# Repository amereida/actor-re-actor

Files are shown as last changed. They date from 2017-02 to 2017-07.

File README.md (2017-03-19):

# actor-re-actor

This repository contains all relevant assets and information for building the **actor-re-actor** unit, a modular device designed for the Athens exhibit of Amereida, entitled 

			**amereida 
			phalène 
			latin (south)
			america**. 

There are 9 of these units.

This work was comissioned as part of the **documenta14** project and realized by the [http://amereida.cl](Open City Group) and [http://ead.pucv.cl](The Shcool of Architecture and Design e[ad], ) [http://www.pucv.cl](Pontificia Universidad Católica de Valparaíso).

### General Shcematics

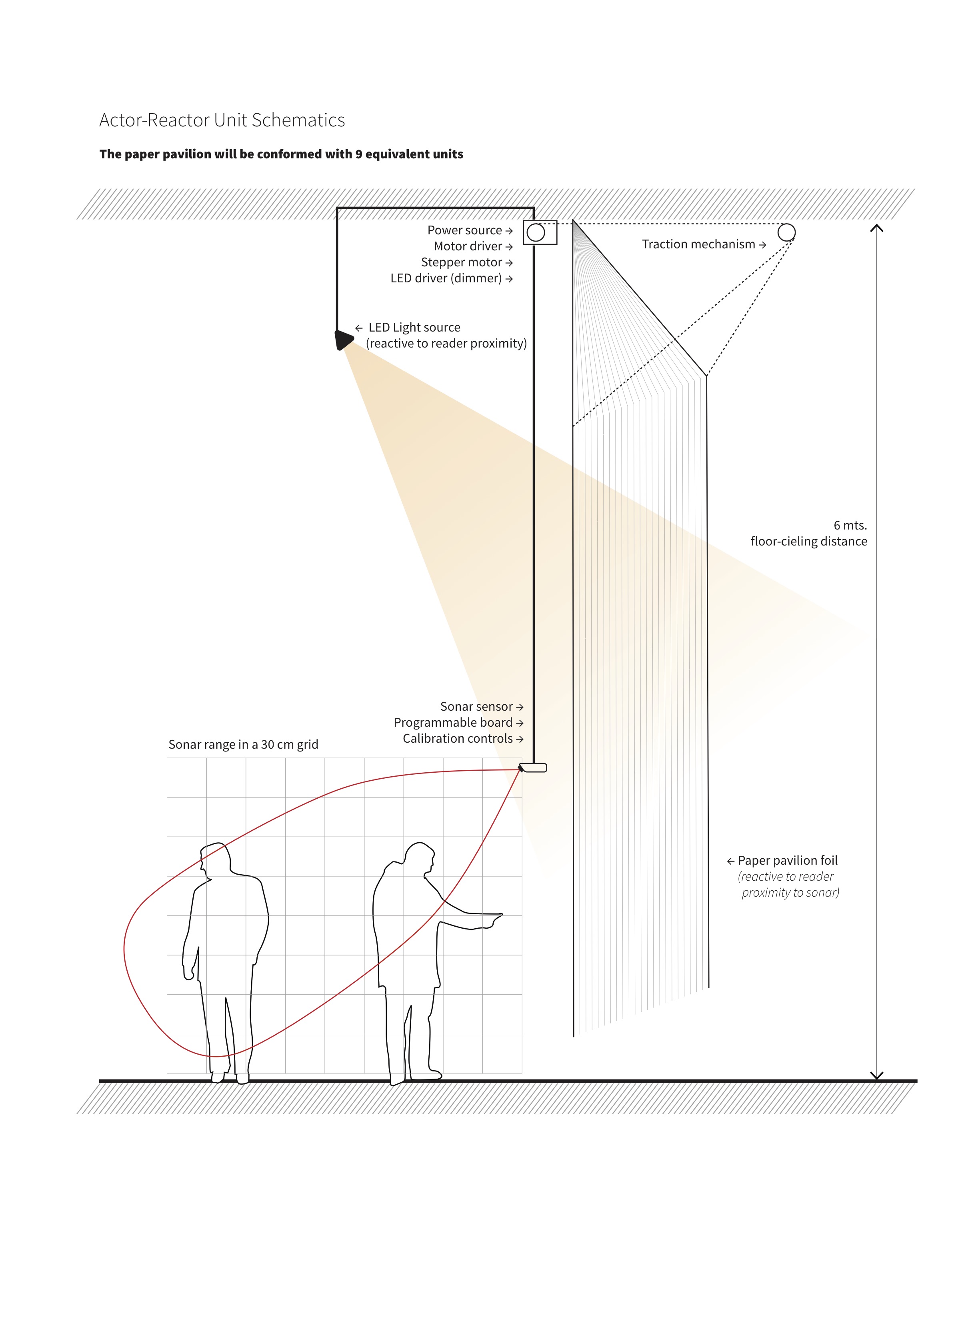
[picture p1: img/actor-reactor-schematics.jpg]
Schema


### Components

1. Actuator Box (inventor files)
	motor-coil (inventor files)
	dimmer (plaques and schematics)
	power & cables (grid)
2. Sensor Box
	Control unit
	Input sensor

### Artistic Statement

     //////////////////////////////////////////////////
     //              //              //              //
     //              //              //              //
     //      1       //       2      //       3      //
     //              //              //              //
     //              //              //              //
     //////////////////////////////////////////////////
     //              //              //              //
     //              //              //              //
     //      4       //       5      //       6      //
     //              //              //              //
     //              //              //              // 
     //////////////////////////////////////////////////
     //              //              //              //
     //              //              //              //
     //      7       //       8      //       9      //
     //              //              //              //
     //              //              //              //     
     //              //              //              //
     //              //              //
     //              //              //

#### 9 Origins, 9 Principles

In this exhibition we ask ourselves for our origin. That is the way of making our content (logos) accessible and open to others, and it is a gesture of hospitality in the first place. Hospitality is a crucial dimension present, from the beginning, in the Open City. Far from being a rhetorical question, we ask ourselves genuinely: what is the sign of our origin? But, at the same time, recognize the multiplicity of this layered, vailed and manifold nature of our inquiry, in the same sense Aristotle warned us: “to on legetai pollachos”, The being is said in many ways; the being is manifold, multiple; it reveals itself in a multiplicity of manners. We choose to beleive in 9.

The paper pavilion, as an exhibit, is structured upon the number nine (9). This number works as a "given" from the poetic word, and no further explanation is (or will be) provided. The number 9 presents itself as a structural totality (and starting point) that will allow us to start working in all that needs to be anticipated and planned relative to the project, all logistics that are required to be defined for this endeavor, but still leaving all the specifics open to be finally resolved in the act of actually building the pavilion. 9 is the way of keeping open that which must be closed.
 
These 9 units have a deep correspondence with all of our activities during our stay in Greece, since our work will be constituted from both 9 poetic acts and the pavilion itself. 9 questions, 9 phalènes, 9 places, 9 gods, 9 games, 9 references, 9 dimensions, etc. And by doing this, all “nines” are clustering in affinity with each other, creating 9 complex and equivalent units, each one developing its own idiosyncratic identity and line of inquiry. These nine are, in concrete, the nine pillars of the paper pavilion, the nine “detentions” for the reader, the nine spot lights for attention, the nine questions to be answered.

The paper foils are automated. There are nine sets of motors and sensors that will define the pavilion’s behavior relative to reader’s proximity, in a merely reactive fashion: no decision will be taken by any algorithm, only a reflex reaction. The paper foils will move as a shy and delicate being that bows in respect and recognition of another’s presence. This is the way in which we want to hardcode hospitality into the space, as a constant bowing and “giving space” to the reader.

Each unit is configured in such a way that if the reader moves closer to the surface, as if he or she wanted to read calmly and in detail, the paper foil will gently move away, as a mirage or an illusion (still reachable at a distance). The sensor placement works as the reference axis, as the (spatial) origin of the unit and will remain unaltered and fixed (anchored). From this referential axis we will hang and present an “original” reference taken from the archive. This configuration will create a relationship between a foreground object composed of a canonical reference and a background surface that will be fruit of the work we will bring from the phalènes (an apollonian figure against a dionysiac background). This relationship will be enhanced by the movement of the reader: the background will move away from the foreground as the point of view moves closer, in the same fashion as the cinematographic dolly-zoom technique, enhancing the tension between foreground (the canonical) and background (the emergent unknown).

The aggregation of these units conforming the pavilion will produce an overall behaviour that will echo the movement of the public, but the reaction will work only from the inside. This configuration will highlight the contrast between being inside and outside, were the people being inside will realize their participation in this ludic coupling between their movement with their surroundings. This will create a sense of complicity, since greater movements will only be achieved in coordination. The reverence of the space (which we earlier called the “bowing” in hospitality may change its character towards a spacing of space, a clearing in the Heideggerian sense of  the “ha lugar” of our poetic standpoint) All these behaviours are direct metaphors that beyond being a figurative gesture they present an autonomous and embodied version of the always-revealing nature of the origin we want to bring into a shared and celebrated presence.

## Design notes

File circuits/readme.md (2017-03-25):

#Component Inventory

- Arduino Nano
- Power Source
- Stepper Motor Nema 23
- Driver Stepper Motor PAP TB6560, 10-35V, +/-3A
- Proximity Sensor, Sonar MB1010
- Dimmer (Specs)

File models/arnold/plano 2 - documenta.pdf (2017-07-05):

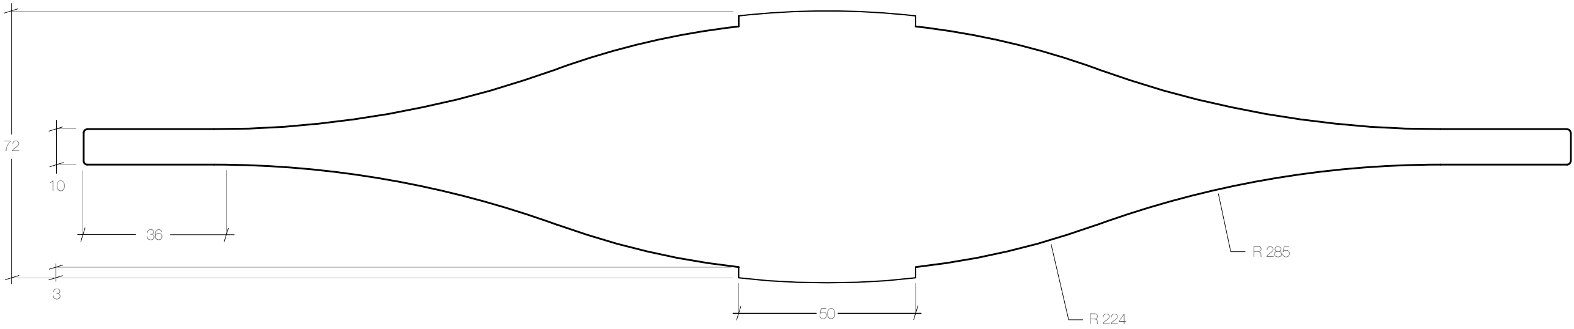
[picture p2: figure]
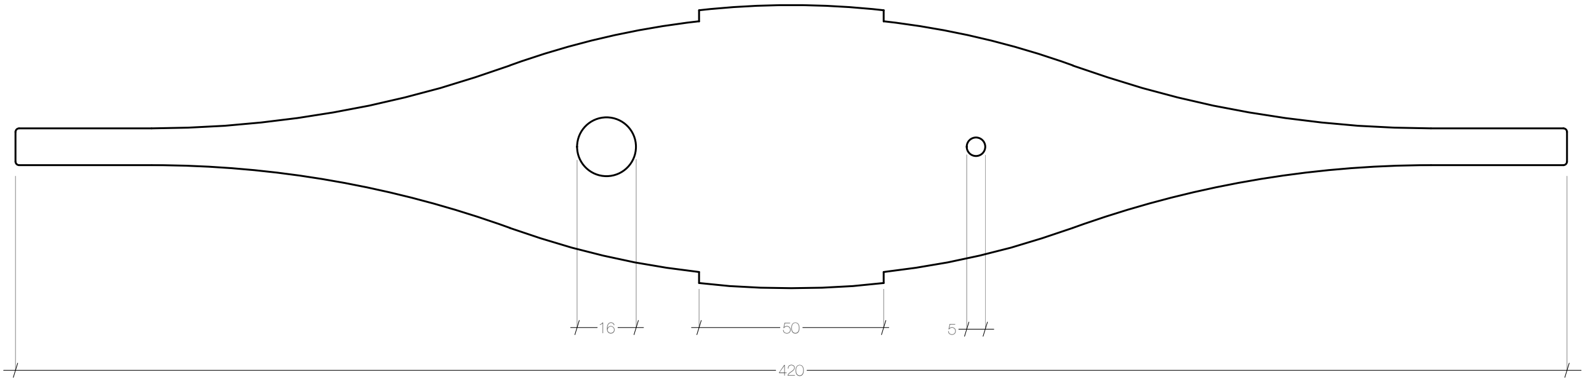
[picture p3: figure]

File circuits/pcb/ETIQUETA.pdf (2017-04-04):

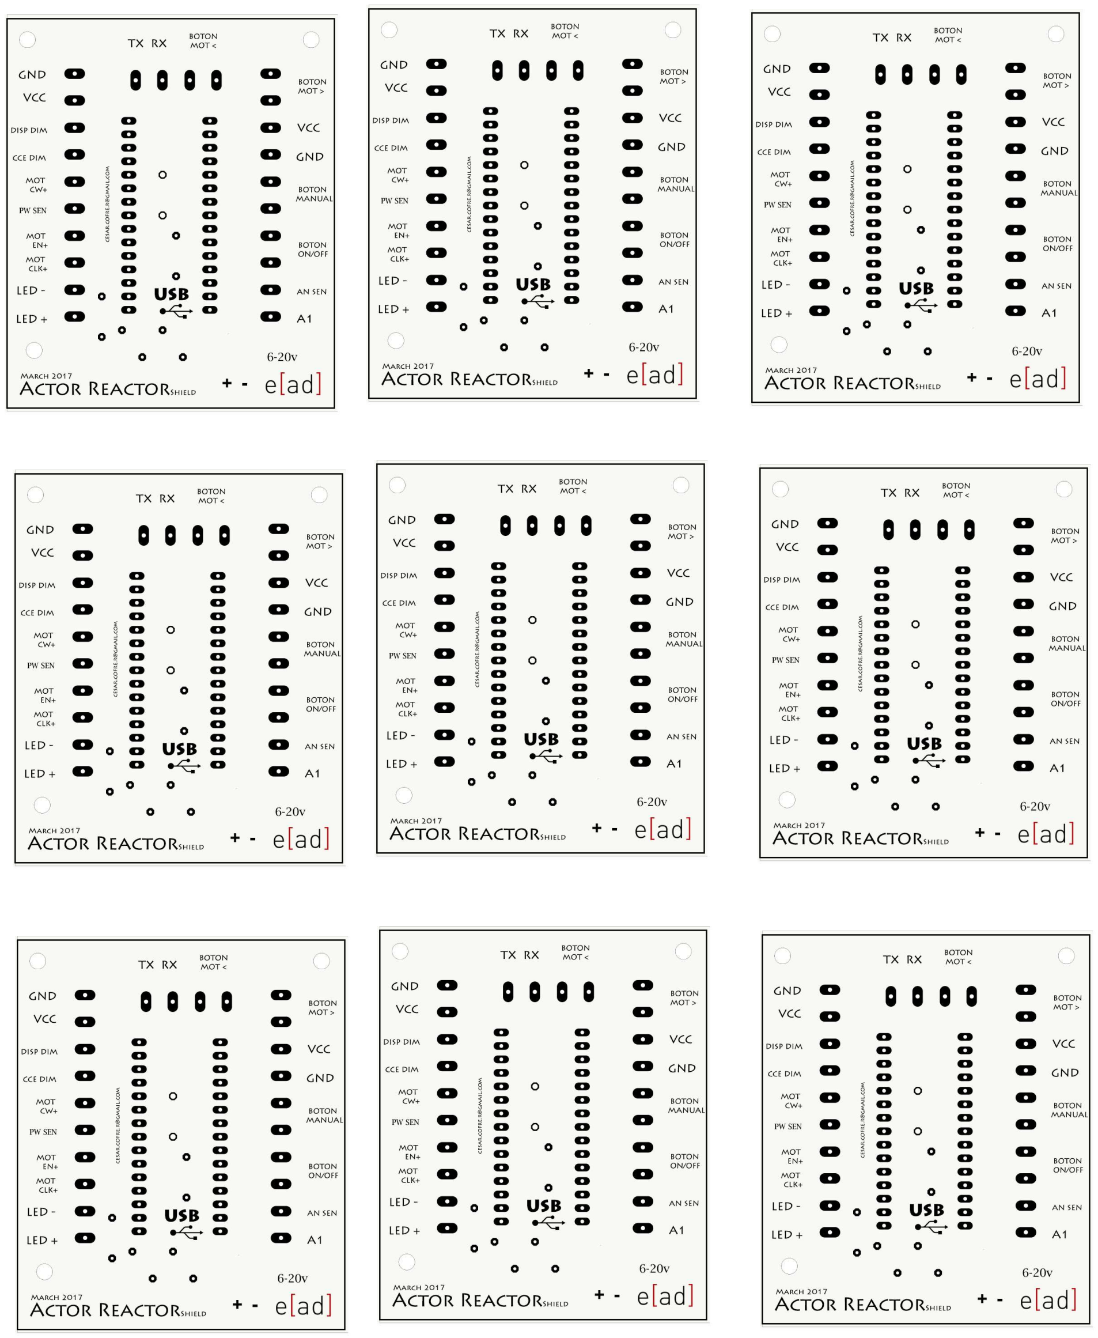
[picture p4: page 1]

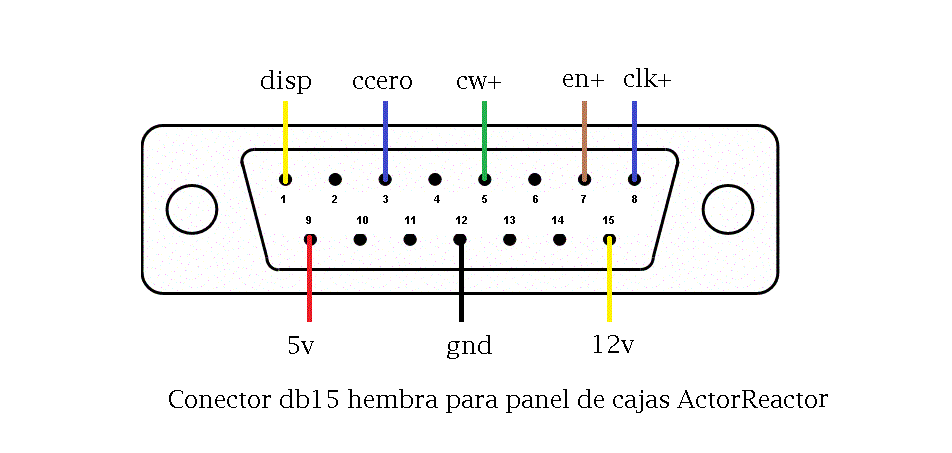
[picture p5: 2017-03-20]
circuits/esquemas/db15hembra_panel_posterior.gif

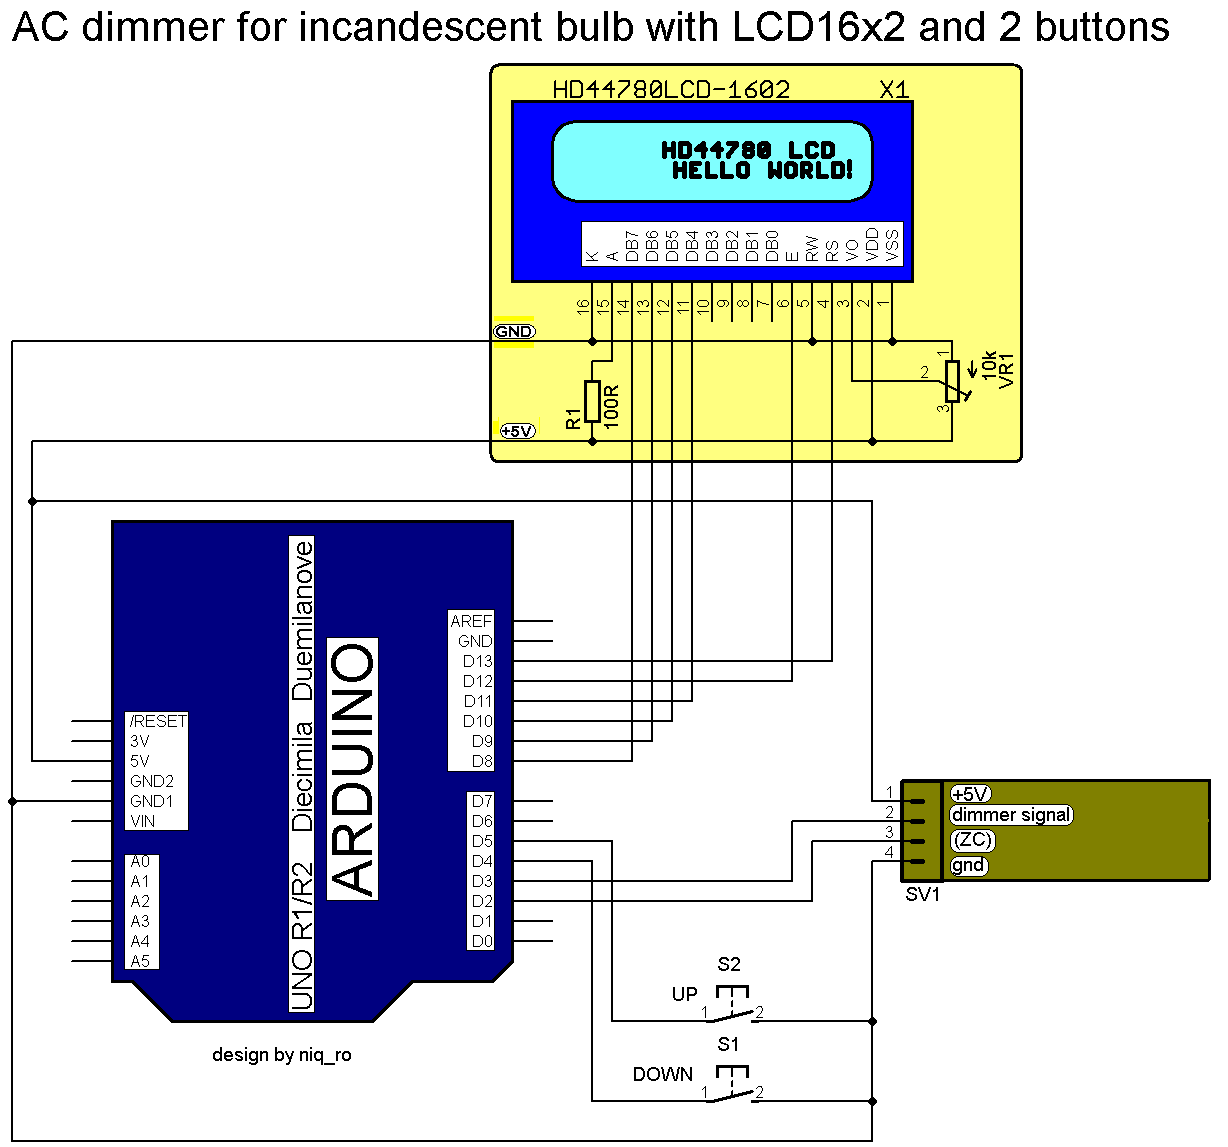
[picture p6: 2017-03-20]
circuits/info/dimmer/Arduinotehniq AC light dimmer with Arduino_files/ac_dimmer1_schematic_arduino_2butons_LCD16x2_rev1.PNG

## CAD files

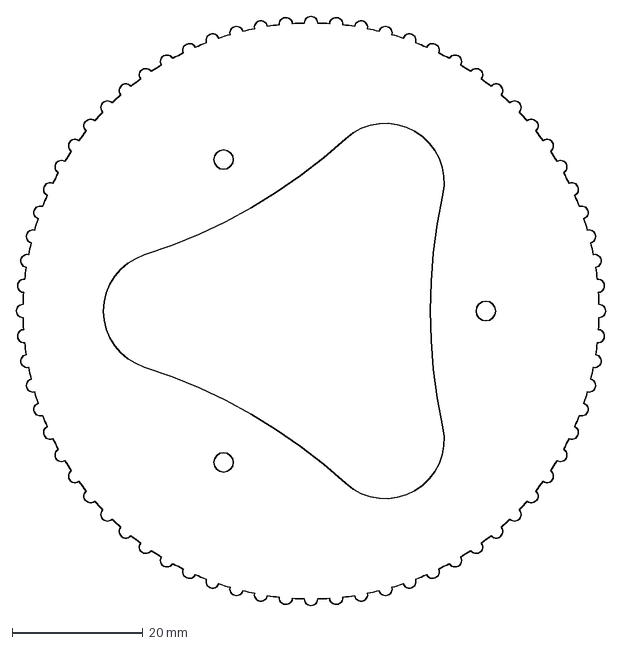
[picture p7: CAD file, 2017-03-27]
models/dxf-laser/engrane para correa 72t.dxf
90.2 x 90.2 mm

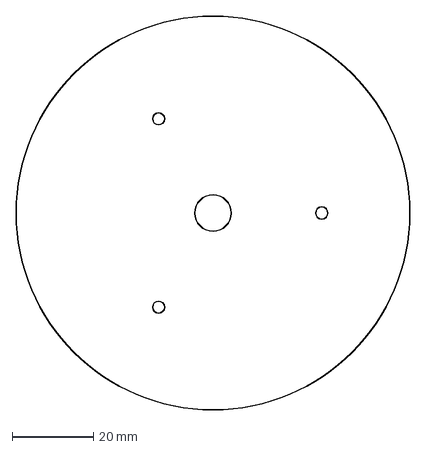
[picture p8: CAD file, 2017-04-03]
models/dxf/tapas polea grande.dxf
96.8 x 96.8 mm

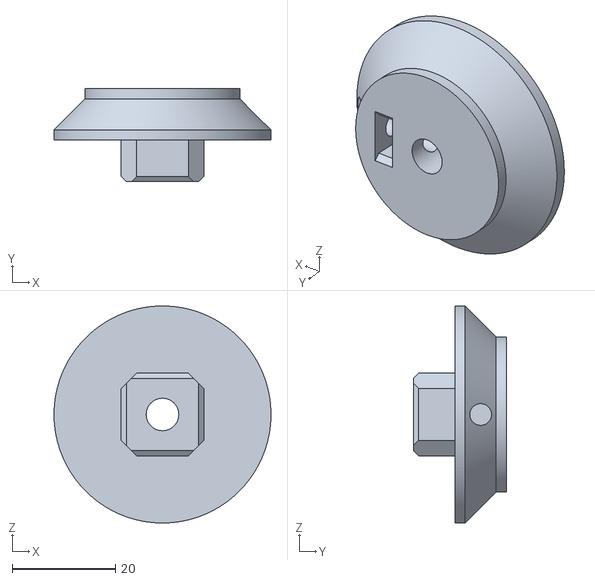
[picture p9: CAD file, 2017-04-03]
models/stl/dado polea correa motor.stl
42.0 x 18.0 x 42.0

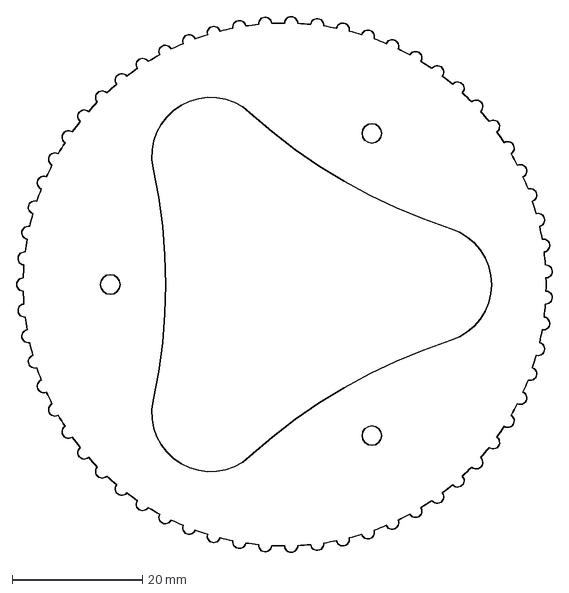
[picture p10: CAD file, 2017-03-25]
models/dxf-laser/engrane plato.dxf
82.3 x 82.3 mm

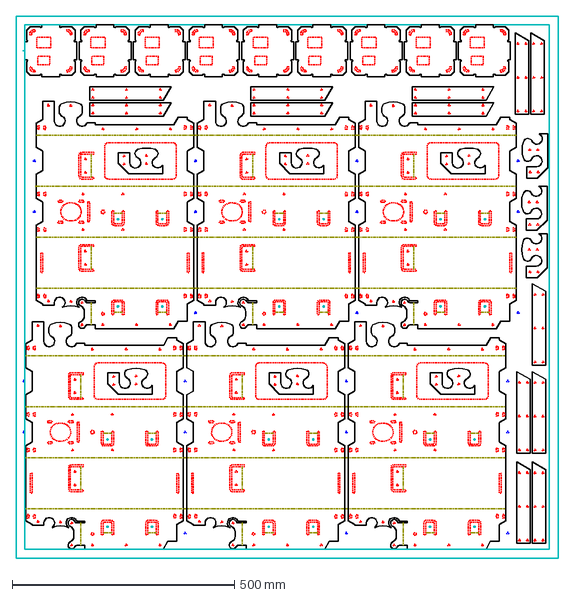
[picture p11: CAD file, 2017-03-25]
models/dxf/plancha2.dxf
1220.0 x 1220.0 mm

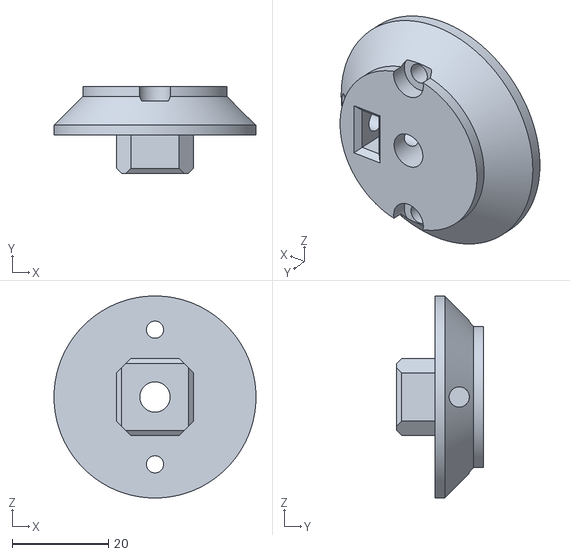
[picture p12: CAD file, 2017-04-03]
models/stl/dado polea correa motor V2.stl
42.0 x 18.0 x 42.0

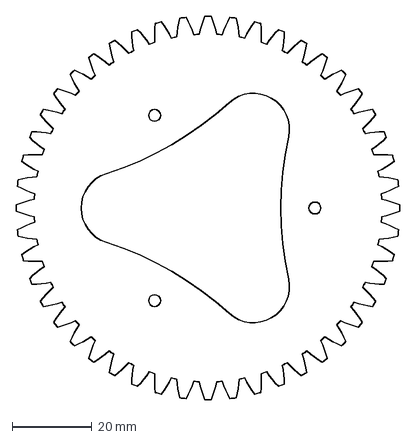
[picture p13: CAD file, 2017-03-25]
models/dxf-laser/engrane carrete.dxf
96.0 x 96.0 mm

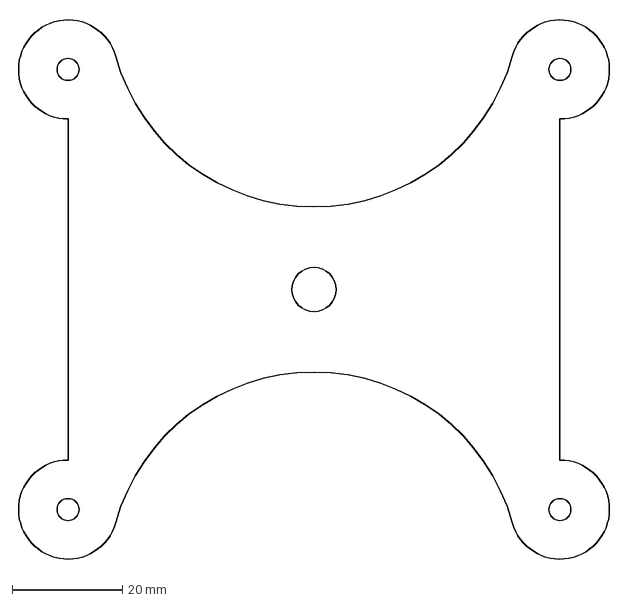
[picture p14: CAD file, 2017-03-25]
models/dxf/protector carrete.dxf
108.2 x 99.4 mm

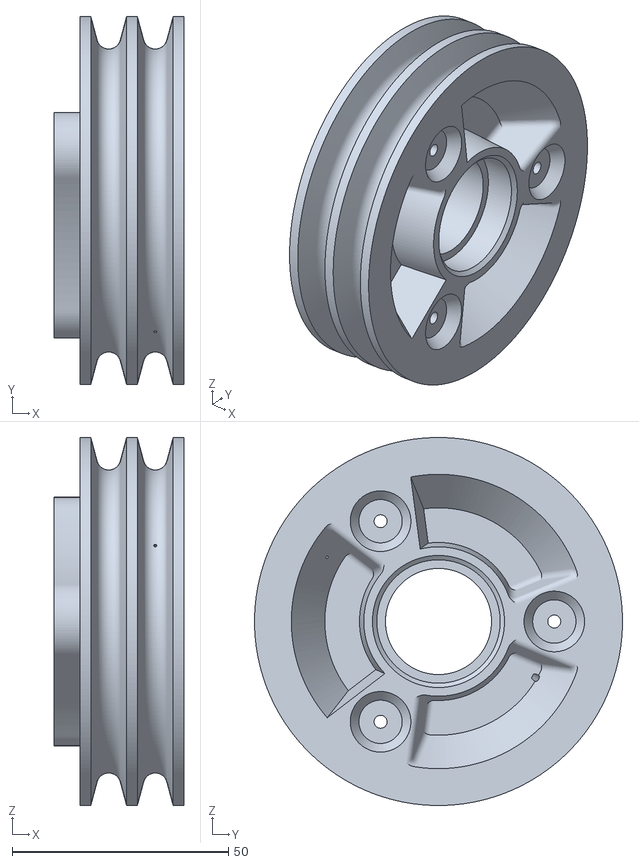
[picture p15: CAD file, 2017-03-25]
models/stl/carrete 85mm.stl
30.0 x 85.0 x 85.0

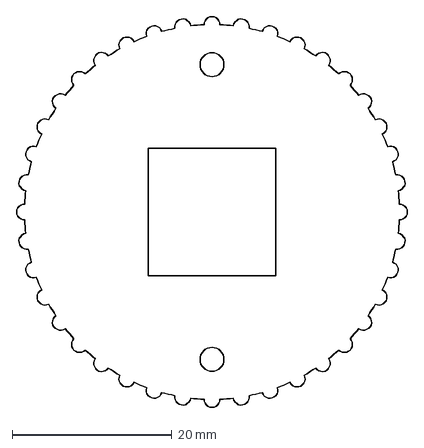
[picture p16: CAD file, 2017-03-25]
models/dxf-laser/polea motor A.dxf
49.0 x 49.0 mm

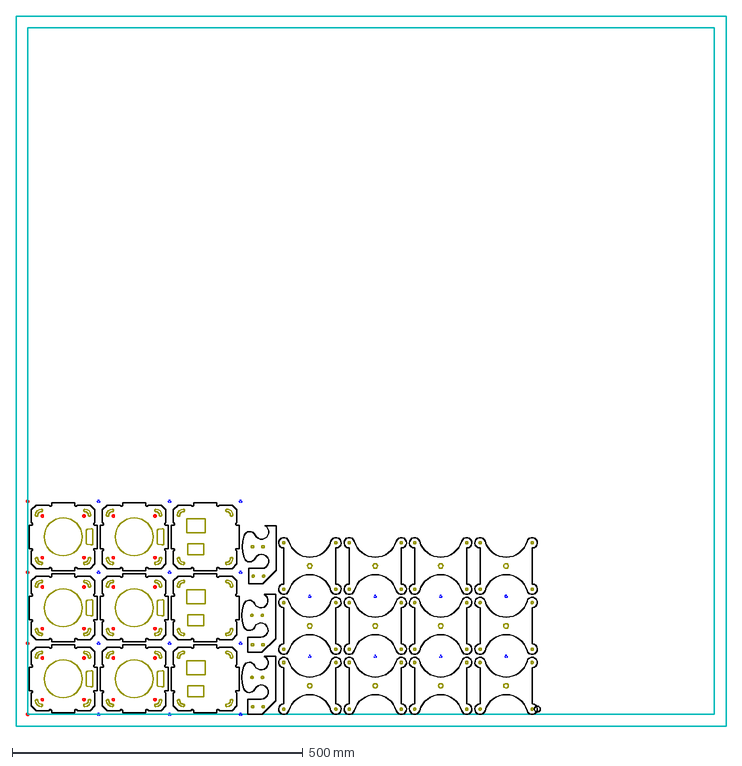
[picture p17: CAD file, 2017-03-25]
models/dxf/plancha3.dxf
1220.0 x 1220.0 mm

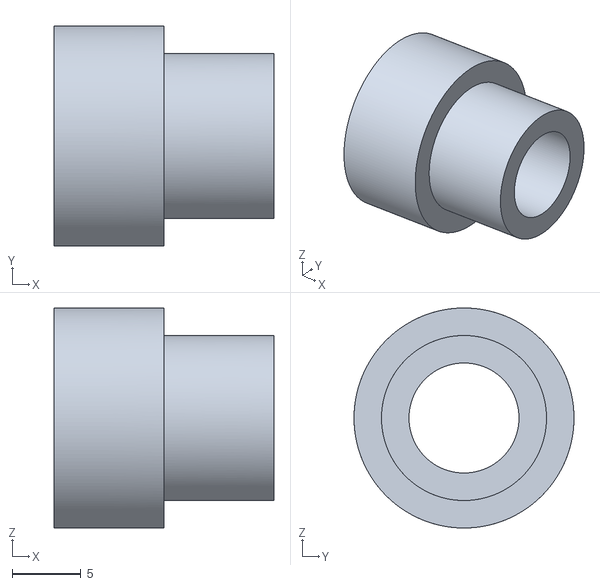
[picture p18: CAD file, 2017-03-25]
models/stl/espaciador mitad.stl
16.0 x 16.0 x 16.0

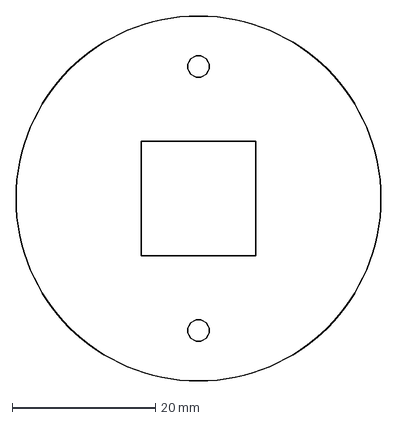
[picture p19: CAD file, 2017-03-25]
models/dxf-laser/polea motor C.dxf
51.0 x 51.0 mm

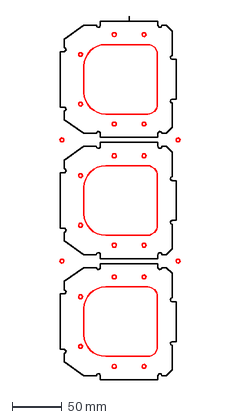
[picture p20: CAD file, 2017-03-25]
models/dxf/refuerzo central correjido.dxf
120.9 x 366.0 mm

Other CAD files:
models/stl/espaciador driver.stl
models/dxf-laser/golilla.dxf
models/dxf/refuerzo central.dxf
models/stl/carrete_base8mm.stl
models/arnold/inventor/pieza baja - documenta.ipt
models/arnold/inventor/pieza frontal - documenta.ipt
models/arnold/inventor/pieza superior - documenta.ipt
models/arnold/inventor/pieza trasera - documenta.ipt
models/dxf-laser/engrane carrete 35°.dxf
models/dxf-laser/engrane polea 35°.dxf
models/dxf-laser/engrane polea.dxf
models/dxf-laser/gg_gear N24 D6 P4 PA35 @100.dxf
models/dxf-laser/gg_gear N48 D12 P4 PA35 @100.dxf
models/dxf-laser/polea grande A.dxf
models/dxf-laser/polea grande B.dxf
models/dxf-laser/polea motor B.dxf
models/dxf/Desarrollo carcasa.dxf
models/dxf/Desarrollo caseC.dxf
models/dxf/Desarrollo.dxf
models/dxf/Planimetrias.dxf
models/dxf/bandeja interior.dxf
models/dxf/cierre remachado 1.dxf
models/dxf/cierre remachado 2.dxf
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

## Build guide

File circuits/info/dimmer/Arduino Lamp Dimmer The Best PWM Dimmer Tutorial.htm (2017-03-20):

DIY Hacking DIY Hacking DIY Hacking DIY Hacking (https://diyhacking.com/)

# Arduino Lamp Dimmer : The Best PWM Dimmer Tutorial

6

23 (https://diyhacking.com/arduino-lamp-dimmer/#comments)

From : Nibodha Technologies

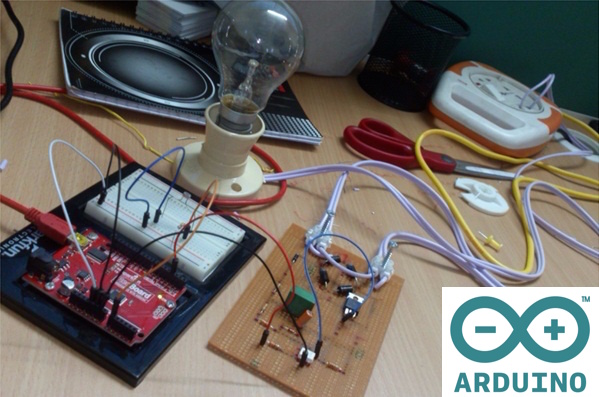
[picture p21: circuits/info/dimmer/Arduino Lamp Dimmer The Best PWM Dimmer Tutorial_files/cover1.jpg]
Arduino lamp dimmer - The best PWM dimmer tutorial
 (https://301o583r8shhildde3s0vcnh-wpengine.netdna-ssl.com/wp-content/uploads/2015/04/cover1.jpg)

Arduino lamp dimmer – The best PWM dimmer tutorial

Ever wondered about how exciting the use of an Arduino board can be in your daily life? We present to you a very basic and a wonderful experiment. We often adjust the display brightness of our mobile phones to suit to our need. Haven’t you felt the same need for your bedside lamps or any other lighting at home? Here we are going to teach you how to make an Arduino lamp dimmer. Using this project, you can control the brightness of your table lamp according to your need. And start building one of the best arduino projects.

What are the stuff required to do this?

1. Arduino
2. Resistors: 330ohm(1No.s), 33k(2no.s), 22k(1No.s), 220ohm(1No.s)
3. Optocoupler: 4N35(1No.s)
4. Diode: 1N4508(4No.s), 1N4007(1No.s), Zener 10V.4W(1No.s)
5. Capacitor 2.2uF/63V(1No.s), 220nF/275V(1No.s)
6. MOSFET: IRF830A
7. Lamp: 100W
8. 230V Supply
9. Socket
10. Solder dot board and Soldering kit

How does it work?

In this project, we are going to adjust the brightness of the lamp connected to the circuit by serial port. The brightness can be changed according to the commands we are providing to the serial port. We will be using these particular commands in this arduino project :

- ‘0’ to TURN OFF.
- ‘1’ for 25% brightness.
- ‘2’ for 50% brightness.
- ‘3’ for 75% brightness.
- ‘4’ for 100% brightness.

We will design a Pulse Wave Modulated (PWM) dimmer circuit which will use IRF830A in a diode bridge which is used to control the voltage across the bulb with pulse wave modulation (PWM). The power supply voltage for driving the gate is supplied by the voltage across the Metal Oxide Semiconductor Field-Effect Transistor (MOSFET).

To know more about MOSFET – click here.

#### Step 1: Circuit for Arduino Lamp Dimmer

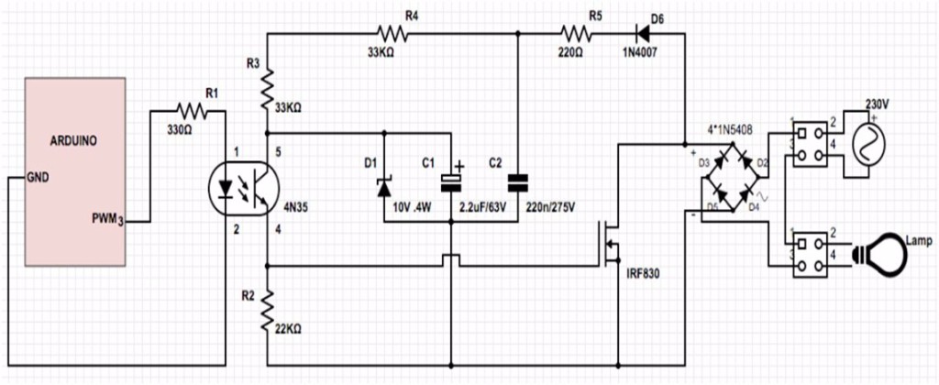
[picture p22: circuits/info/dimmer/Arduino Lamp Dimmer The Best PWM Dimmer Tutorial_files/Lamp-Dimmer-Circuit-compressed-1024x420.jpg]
Arduino lamp dimmer - The best pwm dimmer tutorial
 (https://301o583r8shhildde3s0vcnh-wpengine.netdna-ssl.com/wp-content/uploads/2015/04/Lamp-Dimmer-Circuit-compressed.jpg)

Lamp Dimmer Circuit

The figure clearly explains the positioning of the different electrical components in the circuit. Follow the circuit diagram to solder your dot board.

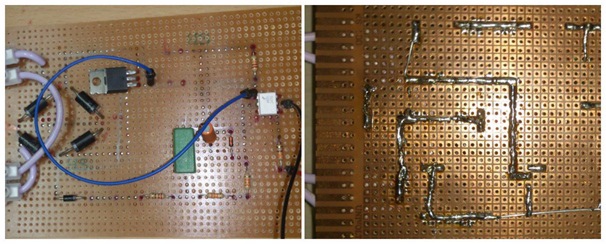
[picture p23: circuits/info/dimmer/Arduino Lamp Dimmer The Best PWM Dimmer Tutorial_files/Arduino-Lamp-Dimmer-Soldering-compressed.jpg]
Arduino Lamp Dimmer Soldering best pwm dimmer tutorial
 (https://301o583r8shhildde3s0vcnh-wpengine.netdna-ssl.com/wp-content/uploads/2015/04/Arduino-Lamp-Dimmer-Soldering-compressed.jpg)

Arduino Lamp Dimmer Soldering

You can use this picture as reference when you solder your board.

To start with, we have the diode D6, the load resistor R5 and the capacitor C2 connected. This forms our rectifier. Also, in the circuit the positioning of the resistor R5 is such that it limits the current pulses through D6 to about 1.5A. This shows that the rectifier is not a pure peak rectifier.

Talking about the capacitor C2, the voltage across it is regulated to a maximum value of 10V by the resistors R3 and R4, capacitor C1 and diode D1.

Optocoupler – http://en.wikipedia.org/wiki/Opto-isolator

The optocoupler and the remaining resistor R2 are used for driving the gate.

The function of R1 is to protect the LED in the optocoupler. Like R5, R1 also limits the current, so that a ‘hard’ voltage can be applied safely. Optocoupler, the CNY65, provides class-II isolation. (Class-II or double insulated electrical appliance is the one which has been designed in such a way that it does not require a safety connection to electrical earth). This is good enough to ensure safety to the regulator.

Now we need the conduction in the MOSFET as quickly as possible. For this, we connect the transistor in the optocoupler to the positive power supply. We have to make a compromise between the switching loss and the inductive voltages as we keep the rating of R2 a bit high, i.e., 22 K-ohm. This is done so as to reduce the switching spikes as a consequence of parasitic inductances.

One additional advantage of the MOSFET is that it helps in the conduction. It conducts for a longer duration than a PWM would do single headedly. Now some interesting information is that when the voltage across the MOSFET reduces, the voltage across D1 remains equal to 10V upon a duty cycle of 88%.

A duty cycle is the percentage of one period up to which a signal is active. A period is the time it takes to complete an on-and-off cycle. The expression for the duty cycle is:

D = (T/P)*100%

Where, D is the duty cycle

T is the time the signal is active

P is the total period of the signal.

A higher duty cycle results in lowering of the voltage. For an instance, at 94% duty cycle, the voltage of 4.8A proved to be just enough to cause the MOSFET to conduct sufficiently. This value is therefore considered as the maximum duty cycle. Also, at this value, the transistor conducts just about cent percent. Measuring with a 100W bulb, the voltage across a 230V mains supply is just 2.5V lower.

Note: We should note that this circuit should not be used to control inductive loads. MOSFET is switched asynchronously and this can cause the DC current to flow.

Now some tips regarding the whole arduino project. Starting off with, we must know that the electronic lamps, such as the PL types, cannot be dimmed with this circuit. This is because these lamps use a rectifier and internally they operate off DC. A few remarks about the value of R3 and R4. This is a compromise between the lowest possible current we consume (when the lamp is off) and the highest possible duty cycle that is allowed. Now as mentioned earlier, the more the duty cycle the less is the voltage. So, we look at a case where the duty cycle is 0%. This results in maximum voltage across the resistors, around 128V across a supply of 230V. Because (depending on the actual resistor) the voltage rating of the resistor may be less than 300 V, two resistors are connected in series. The power that each resistor dissipates amounts to a maximum of 0.5 W. With an eye on the life expectancy, it would be wise to use two 1-W rated resistors here.

#### Step 2 : Uploading the code to Arduino

Here you can see a few more pictures of the finished product.

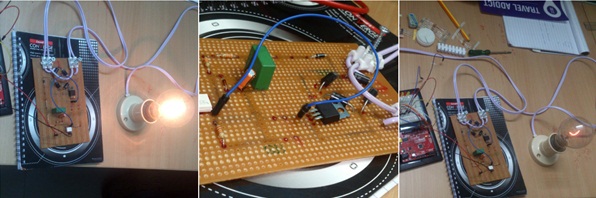
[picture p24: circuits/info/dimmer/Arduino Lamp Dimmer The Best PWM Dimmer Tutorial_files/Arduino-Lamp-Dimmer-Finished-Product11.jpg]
Arduino lamp dimmer - The best pwm dimmer tutorial
 (https://301o583r8shhildde3s0vcnh-wpengine.netdna-ssl.com/wp-content/uploads/2015/04/Arduino-Lamp-Dimmer-Finished-Product11.jpg)

Arduino lamp dimmer

Arduino Script

You can now upload this code to program your Arduino lamp dimmer and start building one of the coolest arduino projects:

intledPin = 3;
void setup()
{
Serial.begin(9600);
Serial.println(“Serial connection started, waiting for instructions…n0 = Offn1 = 25%n2 =50%n3 = 75%n4 = 100%”);
}

void loop ()
{
if (Serial.available()) {
char ser = Serial.read(); //read serial as a character

//NOTE because the serial is read as “char” and not “int”, the read value must be compared to character numbers
//hence the quotes around the numbers in the case statement

switch (ser)
{
case ‘0’:
analogWrite(ledPin, 0);
break;

case ‘1’:
analogWrite(ledPin, 64);
break;

case ‘2’:
analogWrite(ledPin, 128);
break;

case ‘3’:
analogWrite(ledPin, 192);
break;

case ‘4’:
analogWrite(ledPin, 255);
break;
default:
Serial.println(“Invalid entry”);

}
}
}

And now check out the working video for one of the best arduino projects:

Go ahead and make your own Arduino lamp dimmer and get started at domestic electronics :)

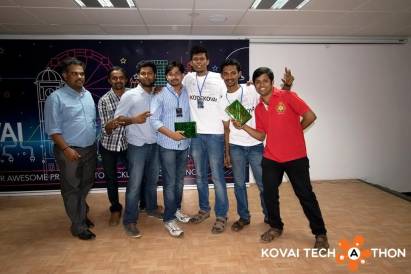
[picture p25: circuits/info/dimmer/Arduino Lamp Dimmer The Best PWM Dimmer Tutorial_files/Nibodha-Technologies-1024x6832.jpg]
Arduino lamp dimmer - The best pwm dimmer tutorial
 (https://301o583r8shhildde3s0vcnh-wpengine.netdna-ssl.com/wp-content/uploads/2015/04/Nibodha-Technologies-1024x6832.jpg)

Nibodha Technologies

– Nibodha Technologies

Nibodha is a Preferred Vacation Rentals Technology Partner. At Nibodha labs, we are actively involved in R&D to solve some of the challenges in Vacation Rental industry using IoT.

We are also the organizers of the Kochi IoT Meetup which is India’s 7th largest IoT meetup group

Tags: AC control (https://diyhacking.com/tag/ac-control/), Arduino (https://diyhacking.com/tag/arduino/), arduino projects (https://diyhacking.com/tag/arduino-projects/), cool arduino projects (https://diyhacking.com/tag/cool-arduino-projects/), home automation (https://diyhacking.com/tag/home-automation/), lamp dimmer (https://diyhacking.com/tag/lamp-dimmer/), pwm (https://diyhacking.com/tag/pwm/), pwm dimmer (https://diyhacking.com/tag/pwm-dimmer/)

Recommended Posts

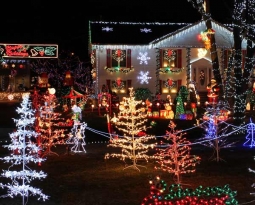
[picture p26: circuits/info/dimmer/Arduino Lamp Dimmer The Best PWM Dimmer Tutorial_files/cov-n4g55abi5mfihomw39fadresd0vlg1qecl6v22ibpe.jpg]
Christmas Light Show with Arduino
-  (https://diyhacking.com/christmas-light-show-with-arduino/)
  Christmas Light Show with Arduino (https://diyhacking.com/christmas-light-show-with-arduino/)
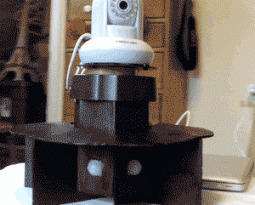
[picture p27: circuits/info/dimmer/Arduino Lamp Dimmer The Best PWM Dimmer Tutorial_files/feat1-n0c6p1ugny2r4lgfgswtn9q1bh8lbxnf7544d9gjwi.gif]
Arduino Security Camera with Motion Tracking: Project Tutorial
-  (https://diyhacking.com/arduino-security-camera/)
  Arduino Security Camera with Motion Tracking: Project Tutorial (https://diyhacking.com/arduino-security-camera/)
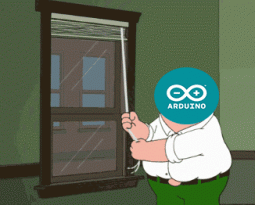
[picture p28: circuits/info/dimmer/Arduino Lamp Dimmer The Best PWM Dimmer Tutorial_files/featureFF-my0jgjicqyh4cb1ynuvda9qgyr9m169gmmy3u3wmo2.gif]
Arduino Curtain Automation: DIY Home Automation Tutorial!
-  (https://diyhacking.com/arduino-curtain-automation/)
  Arduino Curtain Automation: DIY Home Automation Tutorial! (https://diyhacking.com/arduino-curtain-automation/)
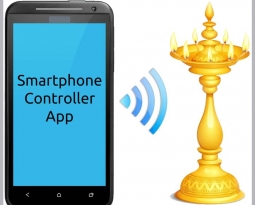
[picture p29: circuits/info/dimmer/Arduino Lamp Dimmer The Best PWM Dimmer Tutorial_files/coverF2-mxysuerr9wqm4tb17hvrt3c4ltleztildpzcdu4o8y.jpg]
DIY Arduino Lamp for Ceremonial Inauguration: Maker Style
-  (https://diyhacking.com/diy-arduino-lamp/)
  DIY Arduino Lamp for Ceremonial Inauguration: Maker Style (https://diyhacking.com/diy-arduino-lamp/)

Showing 23 comments

- 
  Rafael (http://iotgruop.site/) December 26, 2016
  Reply (https://diyhacking.com/arduino-lamp-dimmer/?replytocom=4511#respond)
  can i use it on 60hz 120v?
- 
  diyarduino November 21, 2016
  Reply (https://diyhacking.com/arduino-lamp-dimmer/?replytocom=4269#respond)
  it teach how to fishing. There are some ready circuits online. if you go amazon and search “ac dimmer arduino” you will find great devices. I used one of them in work.
- 
  Denis (http://www.denisgottardello.it/) November 12, 2016
  Reply (https://diyhacking.com/arduino-lamp-dimmer/?replytocom=4203#respond)
  Hi. I have built the board but I have a problem. The lamp is always at 100%. Maybe there is a mistake. Does someone suggest me where could be the problem?
- 
  John October 19, 2016
  Reply (https://diyhacking.com/arduino-lamp-dimmer/?replytocom=4024#respond)
  Hi colleagues,
  Thanks for the log. It is quite interesting. As the upper part seems to be a ac/dc converter, may I connect the 4N35’s pin 5 directly to my DC pin of the arduino and remove the rest of the upper-part components?
  Thanks in advance, John
- 
  Vikas Ambav October 16, 2016
  Reply (https://diyhacking.com/arduino-lamp-dimmer/?replytocom=4003#respond)
  Where is LDR in the circuit? :/
- 
  Prashant Kartikeya October 10, 2016
  Reply (https://diyhacking.com/arduino-lamp-dimmer/?replytocom=3954#respond)
  The circuit works fine for incandescent Bulbs, but CFL bulbs flicker even when the DC side of Opto-coupler is open. Can you please tell me why and how to correct it?
- 
  Abhi September 12, 2016
  Reply (https://diyhacking.com/arduino-lamp-dimmer/?replytocom=3788#respond)
  Please put reference or a link to the source of this circuit. I think this circuit first appeared in elektor.
  There are some drawbacks and there are some methods to overcome those drawbacks. Please include them also.
- 
  Gautam (http://www.goclabs.com/) September 1, 2016
  Reply (https://diyhacking.com/arduino-lamp-dimmer/?replytocom=3733#respond)
  can we run ceiling fan with this circuit??
- 
  Akshay August 16, 2016
  Reply (https://diyhacking.com/arduino-lamp-dimmer/?replytocom=3631#respond)
  Hi.. Can I use this circuit with raspberry pi?? anybody tried using rasp pi and controlled led light?
- 
  nidhi June 9, 2016
  Reply (https://diyhacking.com/arduino-lamp-dimmer/?replytocom=3276#respond)
  how do you power the Arduino ?
- 
  hugo May 24, 2016
  Reply (https://diyhacking.com/arduino-lamp-dimmer/?replytocom=3177#respond)
  what would i do if i don’t have the MOSFET: IRF830A?, what mosfet recommendme?
- 
  Bill Loney February 28, 2016
  Reply (https://diyhacking.com/arduino-lamp-dimmer/?replytocom=2563#respond)
  If I could understand what you’re trying to say that would be okay… I’m a term 5 electrical engineering student and I still don’t understand. I am a white male, 200 lbs, completely lucid. Thank you for your time.
- 
  Rudy February 26, 2016
  Reply (https://diyhacking.com/arduino-lamp-dimmer/?replytocom=2537#respond)
  man, please, can you show us the coding from the video please….
- 
  anthony February 14, 2016
  Reply (https://diyhacking.com/arduino-lamp-dimmer/?replytocom=2461#respond)
  Will this work with 10watt led? if so what modification will I do to dim 4 of them? 4 led will be in-synch
- 
  kees February 5, 2016
  Reply (https://diyhacking.com/arduino-lamp-dimmer/?replytocom=2389#respond)
  It is an old Elektor design from Ton Giesberts and has some drawbacks https://arduinodiy.wordpress.com/2015/07/25/1498/
- 
  akekec February 4, 2016
  Reply (https://diyhacking.com/arduino-lamp-dimmer/?replytocom=2383#respond)
  LDR is used in the video. But there is no LDR in software. Can I be wrong.
- 
  akekec February 4, 2016
  Reply (https://diyhacking.com/arduino-lamp-dimmer/?replytocom=2382#respond)
  http://diyhacking.com/arduino-lamp-dimmer/
- 
  Paul December 18, 2015
  Reply (https://diyhacking.com/arduino-lamp-dimmer/?replytocom=2013#respond)
  http://www.instructables.com/id/safe-and-simple-AC-PWM-Dimmer-for-arduino-Raspberr/
- 
  Francesco December 6, 2015
  Reply (https://diyhacking.com/arduino-lamp-dimmer/?replytocom=1914#respond)
  Hi, I’m a newbie, so I’m sorry if I’m not able to debug it by myself. I can’t get the circuit to work, can you please post more detailed photos so I can make sure that I’m doing everything correctly? Thanks a lot!
  - 
    Rudy January 26, 2016
    Reply (https://diyhacking.com/arduino-lamp-dimmer/?replytocom=2309#respond)
    hi man, do you get the detailed picture yet? would you share it with me? thanks so much man…
- 
  Lucas June 26, 2015
  Reply (https://diyhacking.com/arduino-lamp-dimmer/?replytocom=1381#respond)
  Mine works but flickers once I set the duty cycle. Any advise?
- 
  js2002 June 12, 2015
  Reply (https://diyhacking.com/arduino-lamp-dimmer/?replytocom=1365#respond)
  Hi man,
  I suggest to add simple LC or RC filter to reduce RF emitting.
  Best regrads,
  Jiri
- 
  Bruno May 14, 2015
  Reply (https://diyhacking.com/arduino-lamp-dimmer/?replytocom=1232#respond)
  Hello man, I’m using your circuit with a raspberry pi, and it works great, but I have a problem, when I set the maximum light intensity, the bulb and the IRF830 starts to burn, what can I do?
  Best Regards

### Leave a Comment

Math Captcha
+ 77 = 82

Follow Us

(https://www.facebook.com/diyhacking) (https://twitter.com/DIYhacking) (https://www.youtube.com/channel/UC6G4RDruQIPufKH-NLbXwAA)

Recent Posts

- Christmas Light Show with Arduino (https://diyhacking.com/christmas-light-show-with-arduino/)
  Christmas Light Show with Arduino (https://diyhacking.com/christmas-light-show-with-arduino/)
- Rendering Light and Shadow with Unity for Augmented Reality (https://diyhacking.com/rendering-light-and-shadow-unity/)
  Rendering Light and Shadow with Unity for Augmented Reality (https://diyhacking.com/rendering-light-and-shadow-unity/)
- Getting Started with GitHub in 7 Minutes (https://diyhacking.com/getting-started-with-github/)
  Getting Started with GitHub in 7 Minutes (https://diyhacking.com/getting-started-with-github/)
- PCB Basics Tutorial: A Must-Read for Beginners (https://diyhacking.com/pcb-basics-tutorial/)
  PCB Basics Tutorial: A Must-Read for Beginners (https://diyhacking.com/pcb-basics-tutorial/)
- Augmented Reality Tutorial for making a Pokemon Game using Vuforia (https://diyhacking.com/augmented-reality-tutorial-pokemon/)
  Augmented Reality Tutorial for making a Pokemon Game using Vuforia (https://diyhacking.com/augmented-reality-tutorial-pokemon/)

Categories

- 3D Designing (https://diyhacking.com/category/3ddesign/)
- Advanced (https://diyhacking.com/category/advanced/)
- Arduino projects (https://diyhacking.com/category/arduino-projects/)
- Beginners (https://diyhacking.com/category/beginners/)
- Blog (https://diyhacking.com/category/blog/)
- Cyber Security (https://diyhacking.com/category/cybersecurity/)
- Drones (https://diyhacking.com/category/diy-drones/)
- eBooks (https://diyhacking.com/category/ebooks/)
- Electronics hacks (https://diyhacking.com/category/electronics-hacks/)
- Intel Edison (https://diyhacking.com/category/intel-edison/)
- Intermediate (https://diyhacking.com/category/intermediate/)
- Raspberry pi projects (https://diyhacking.com/category/raspberrypi-projects/)
- Robotics (https://diyhacking.com/category/robotics/)
- Uncategorized (https://diyhacking.com/category/uncategorized/)
- VR and AR (https://diyhacking.com/category/vr-ar/)

© EETech Media, LLC. All rights reserved. Unauthorized use and/or duplication of this material without express and written permission from the author and/or owner is strictly prohibited. Links to this site may be used, provided that full and clear credit is given to DIYHacking.com with appropriate and specific direction to the original content.

Start typing and press Enter to search

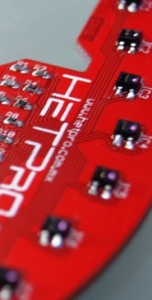
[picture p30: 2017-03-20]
circuits/info/driver de motor pap TB6560/TB6560 Controlador Motor a Pasos - Tutoriales HeTPro _ HETPRO_TUTORIALES_files/analog-152x300.jpg

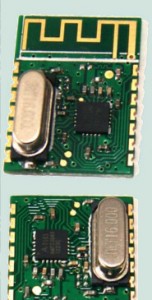
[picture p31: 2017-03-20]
circuits/info/driver de motor pap TB6560/TB6560 Controlador Motor a Pasos - Tutoriales HeTPro _ HETPRO_TUTORIALES_files/rf-152x300.jpg

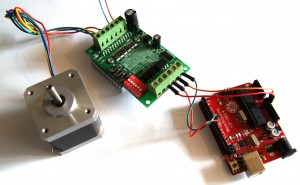
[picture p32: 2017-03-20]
circuits/info/driver de motor pap TB6560/TB6560 Controlador Motor a Pasos - Tutoriales HeTPro _ HETPRO_TUTORIALES_files/tmap_001-1-300x185.jpg

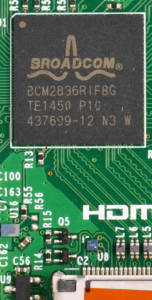
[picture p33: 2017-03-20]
circuits/info/driver de motor pap TB6560/TB6560 Controlador Motor a Pasos - Tutoriales HeTPro _ HETPRO_TUTORIALES_files/raspberry-152x300.png

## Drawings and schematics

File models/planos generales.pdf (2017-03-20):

## ensamble caja motriz

1 : 2

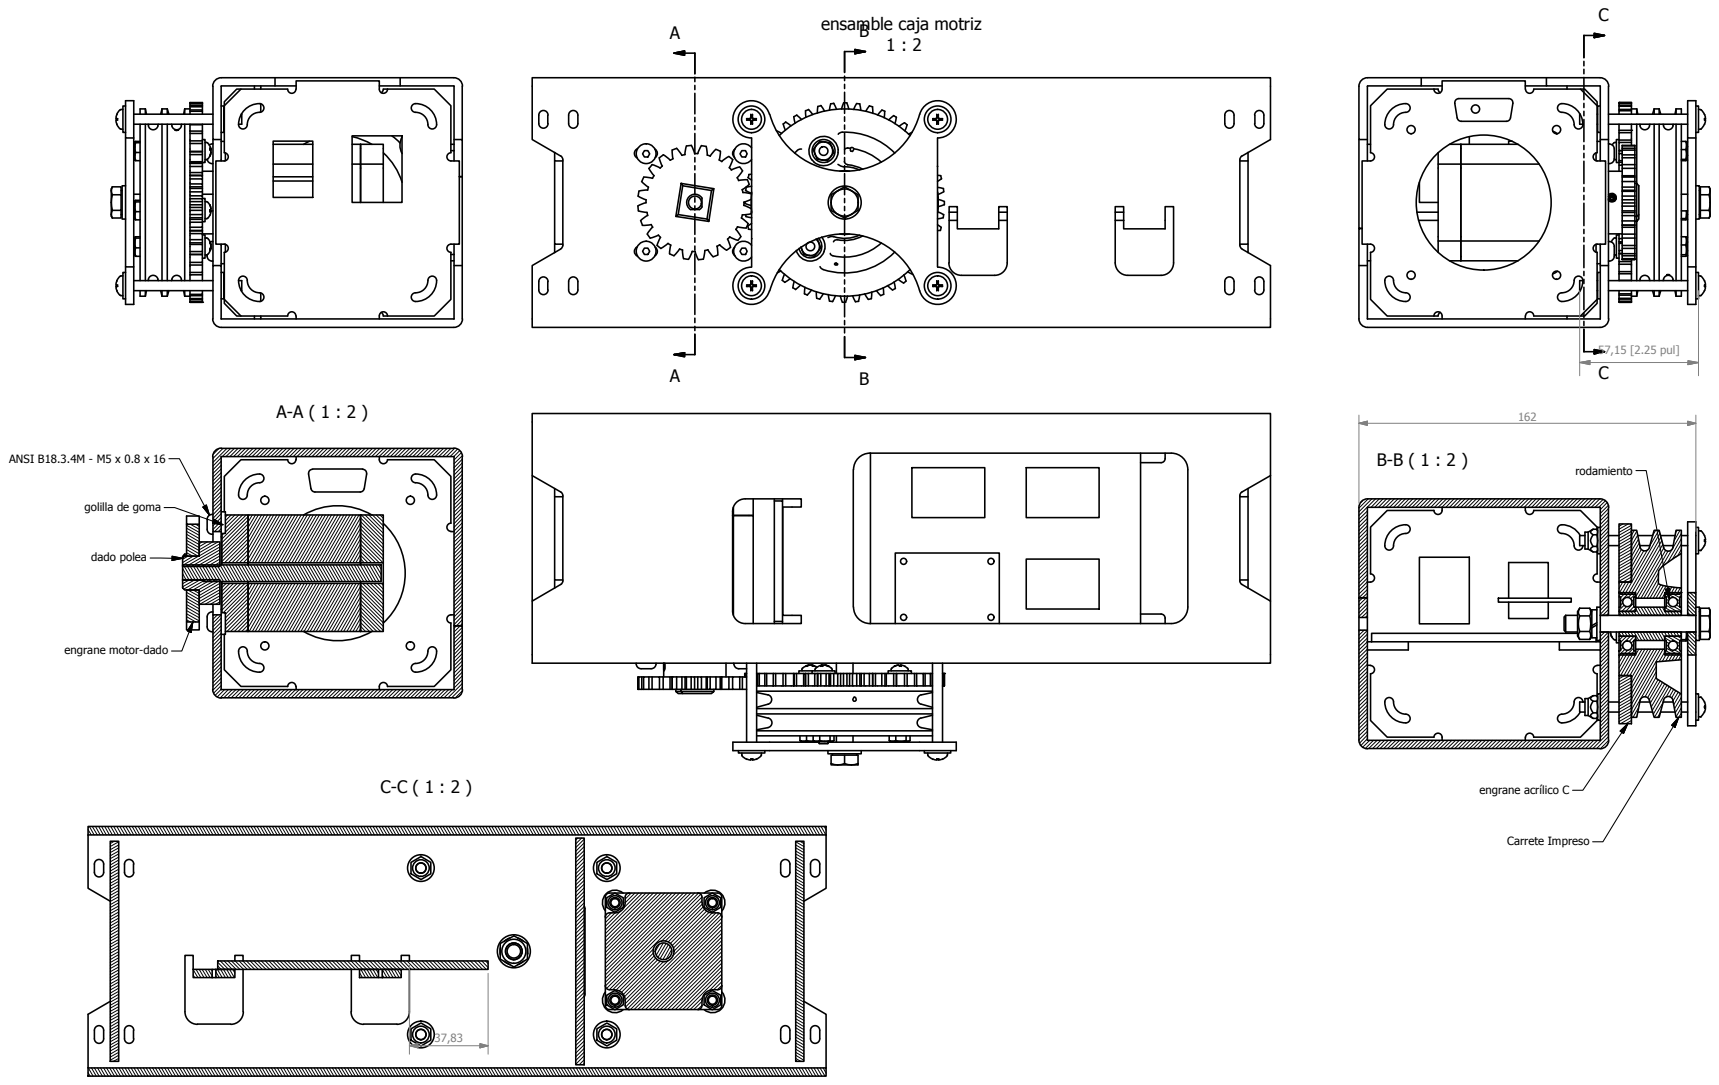
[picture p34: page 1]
engrane acrtlico C; Carrete Impreso; rodamiento; dado polea; ANSI B18.3.4M - M5 x 0.8 x 16; 57,15 [2.25 pul]

golilla de goma

engrane motor-dado

e

n

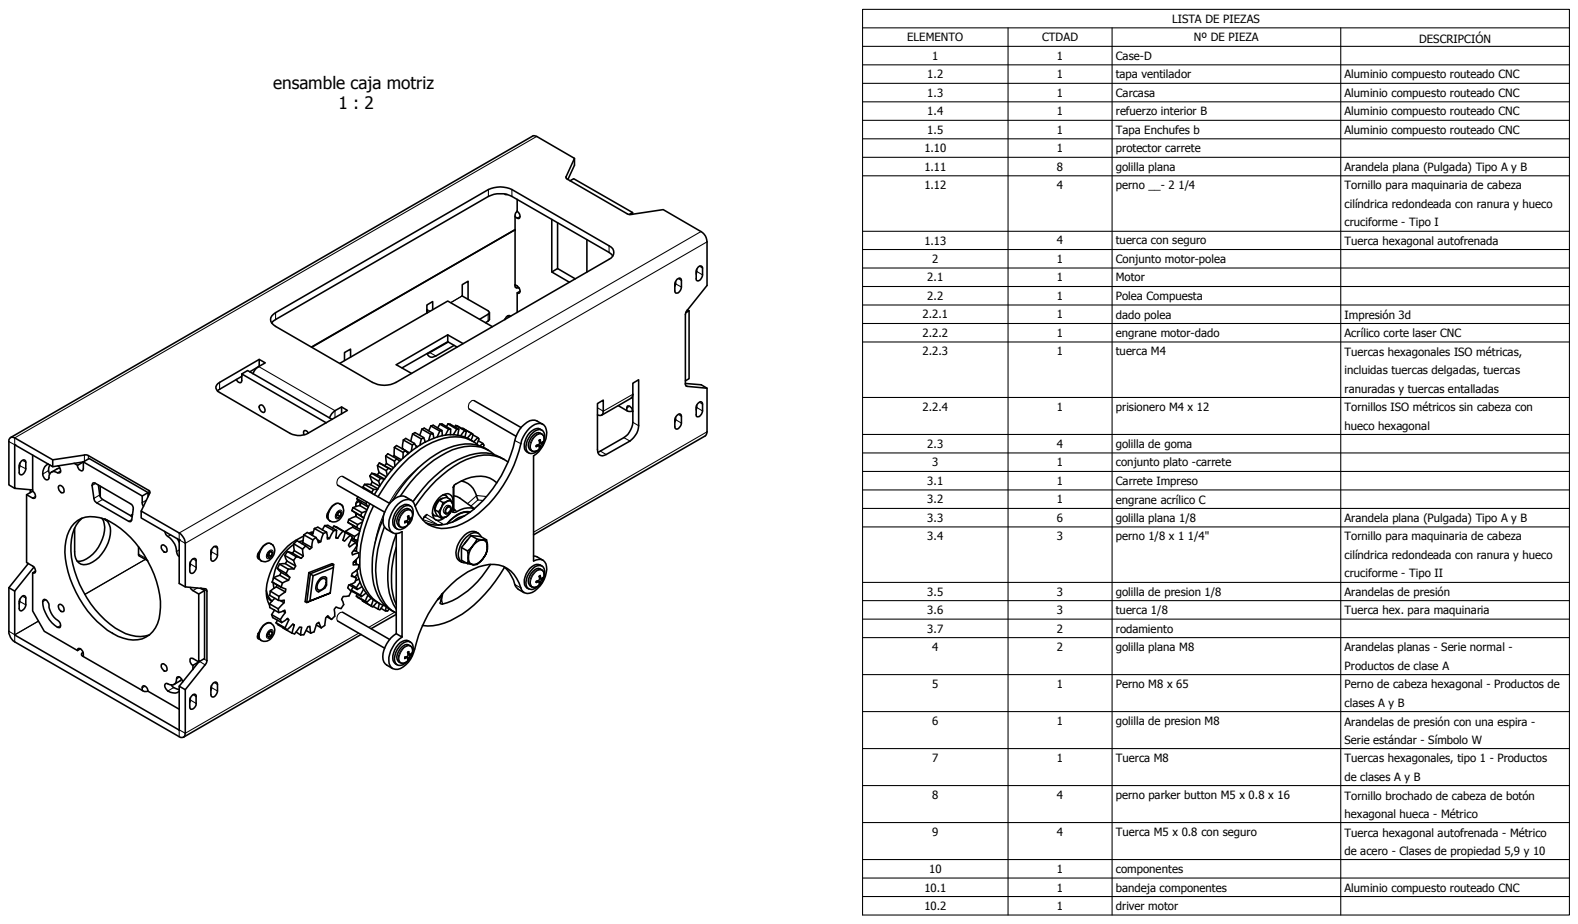
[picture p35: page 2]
ble; ila; Alu; olilla; pla; ela; ulg; illo; ilt n; ole; tli c; ale; clu; elg; alla; prisionero M4 x 12 2.3; golilla de goma 3; conjunto plato -carrete 3.1; Carrete Impreso 3.2; engrane acrtlico C 3.3; golilla plana 1/8; Arandela plana (P; cla; olo; Cla

## Isomptrica montaje motor

1 : 2

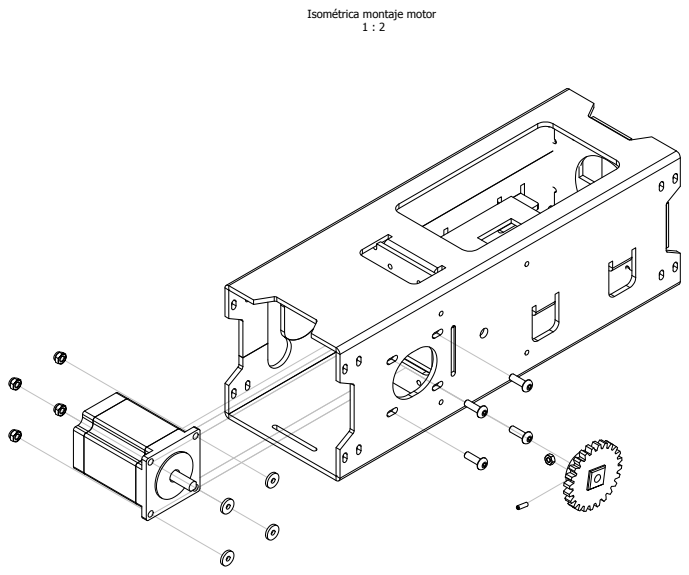
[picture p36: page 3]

## isometrica montaje carrete

1 : 2

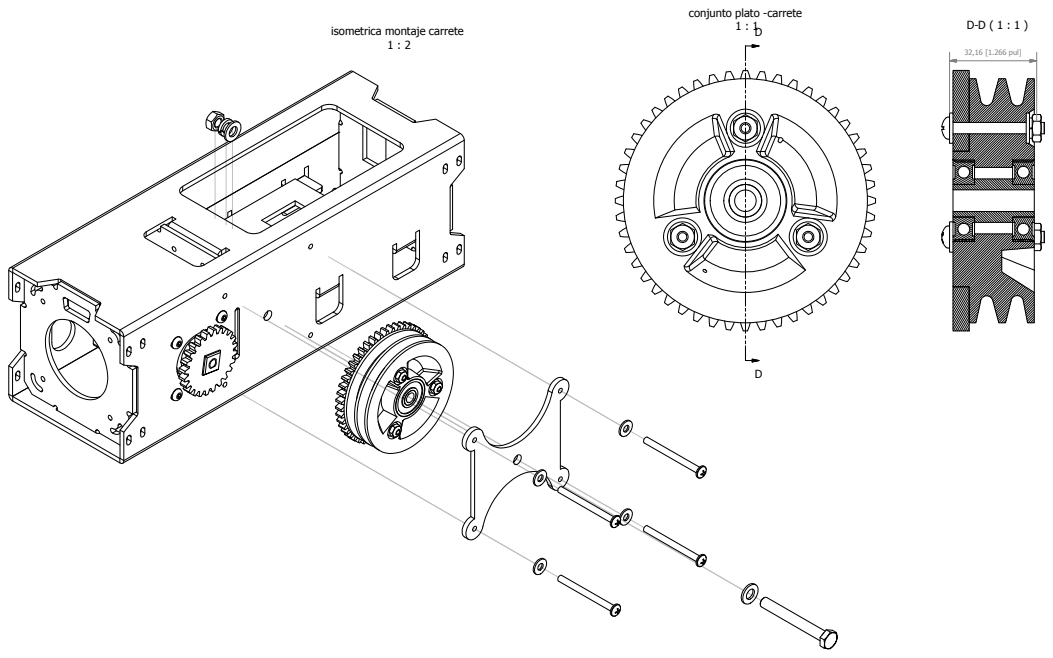
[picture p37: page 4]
32,16 [1.266 pul]

conjunto plato -carrete

## Montaje componentes electrynicos

1 : 2

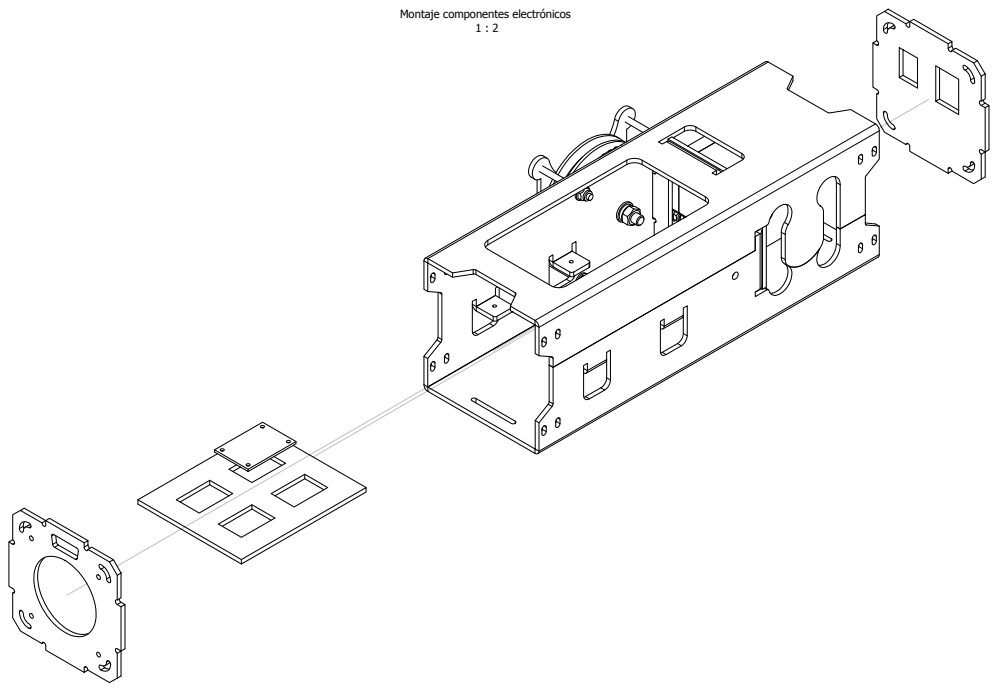
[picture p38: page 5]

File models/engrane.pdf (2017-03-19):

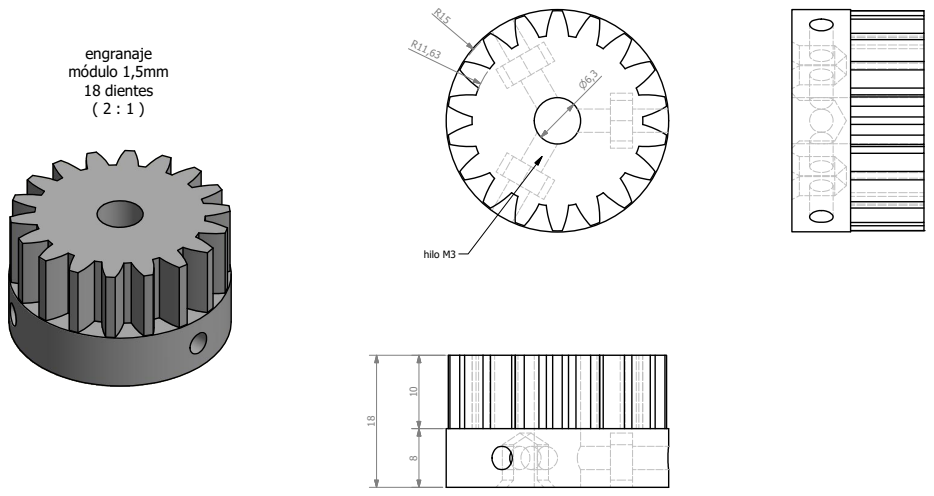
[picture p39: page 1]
engranaje mydulo 1,5mm 18 dientes ( 2 : 1 ); hilo M3

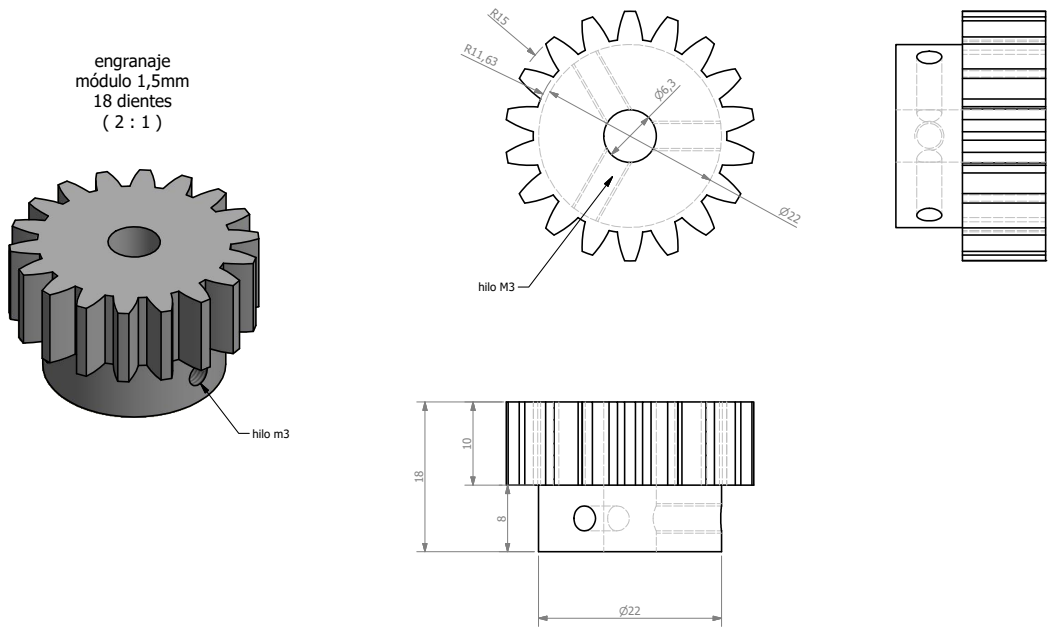
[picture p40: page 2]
engranaje mydulo 1,5mm 18 dientes ( 2 : 1 ); hilo M3; hilo m3

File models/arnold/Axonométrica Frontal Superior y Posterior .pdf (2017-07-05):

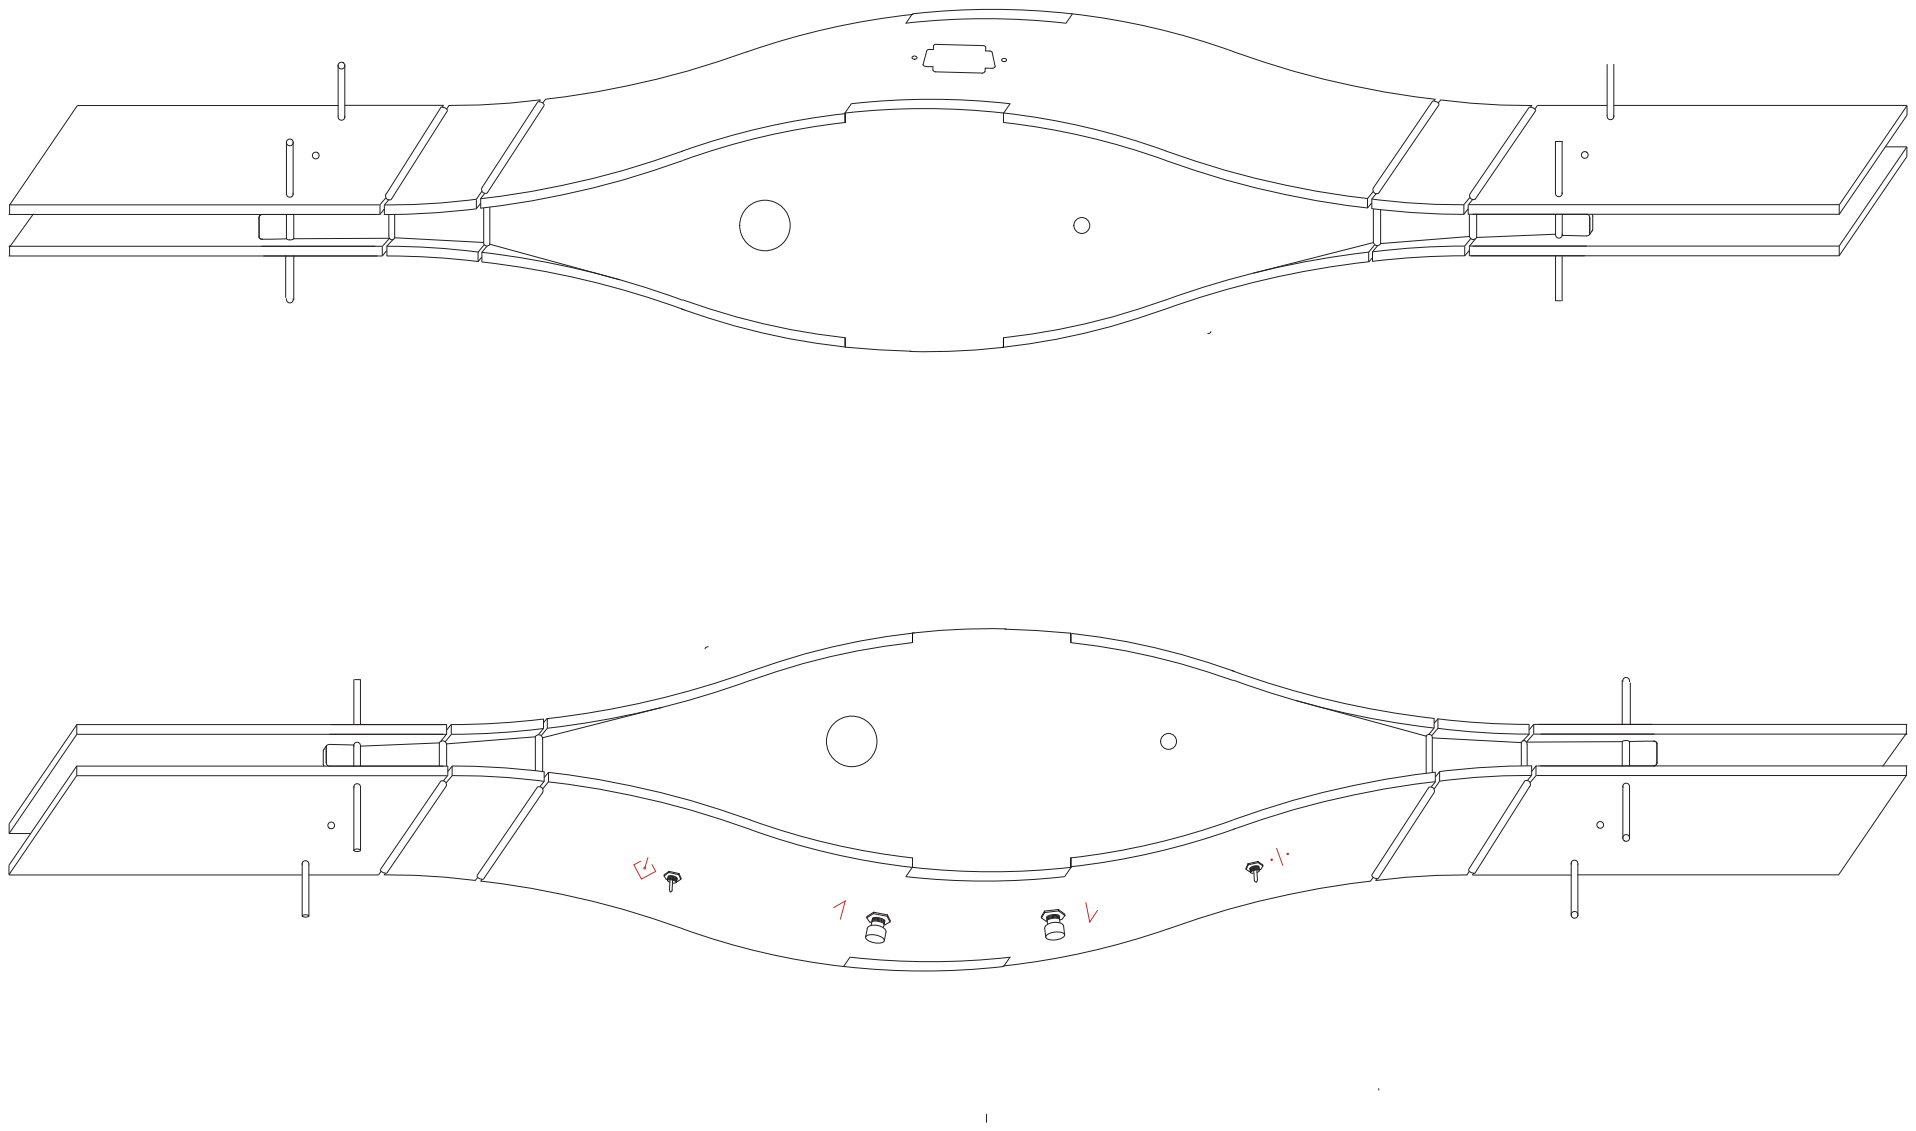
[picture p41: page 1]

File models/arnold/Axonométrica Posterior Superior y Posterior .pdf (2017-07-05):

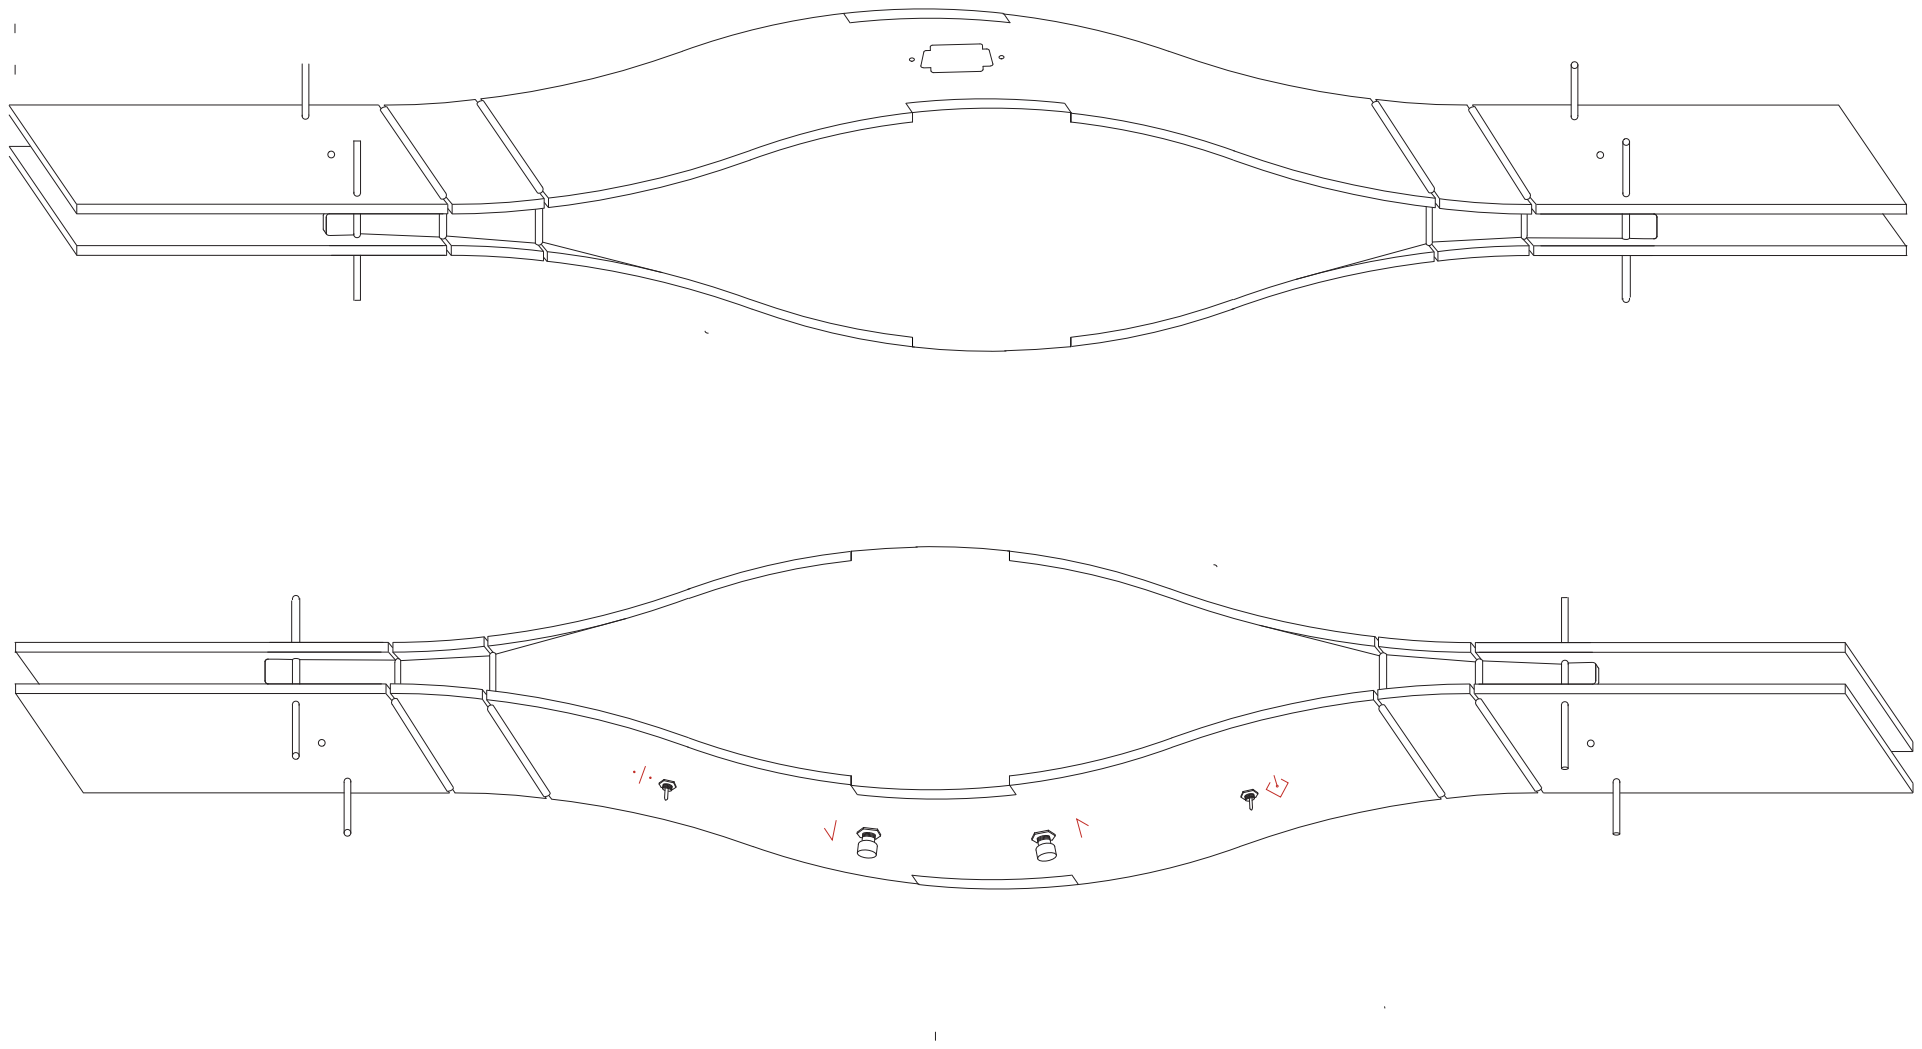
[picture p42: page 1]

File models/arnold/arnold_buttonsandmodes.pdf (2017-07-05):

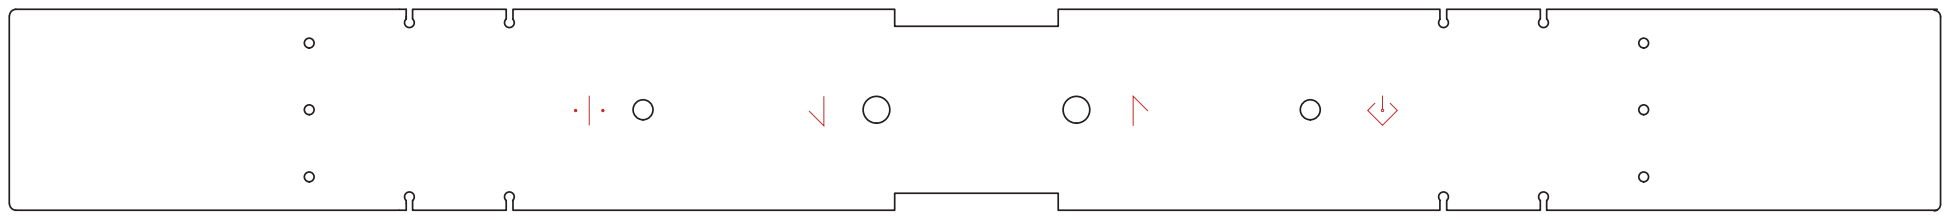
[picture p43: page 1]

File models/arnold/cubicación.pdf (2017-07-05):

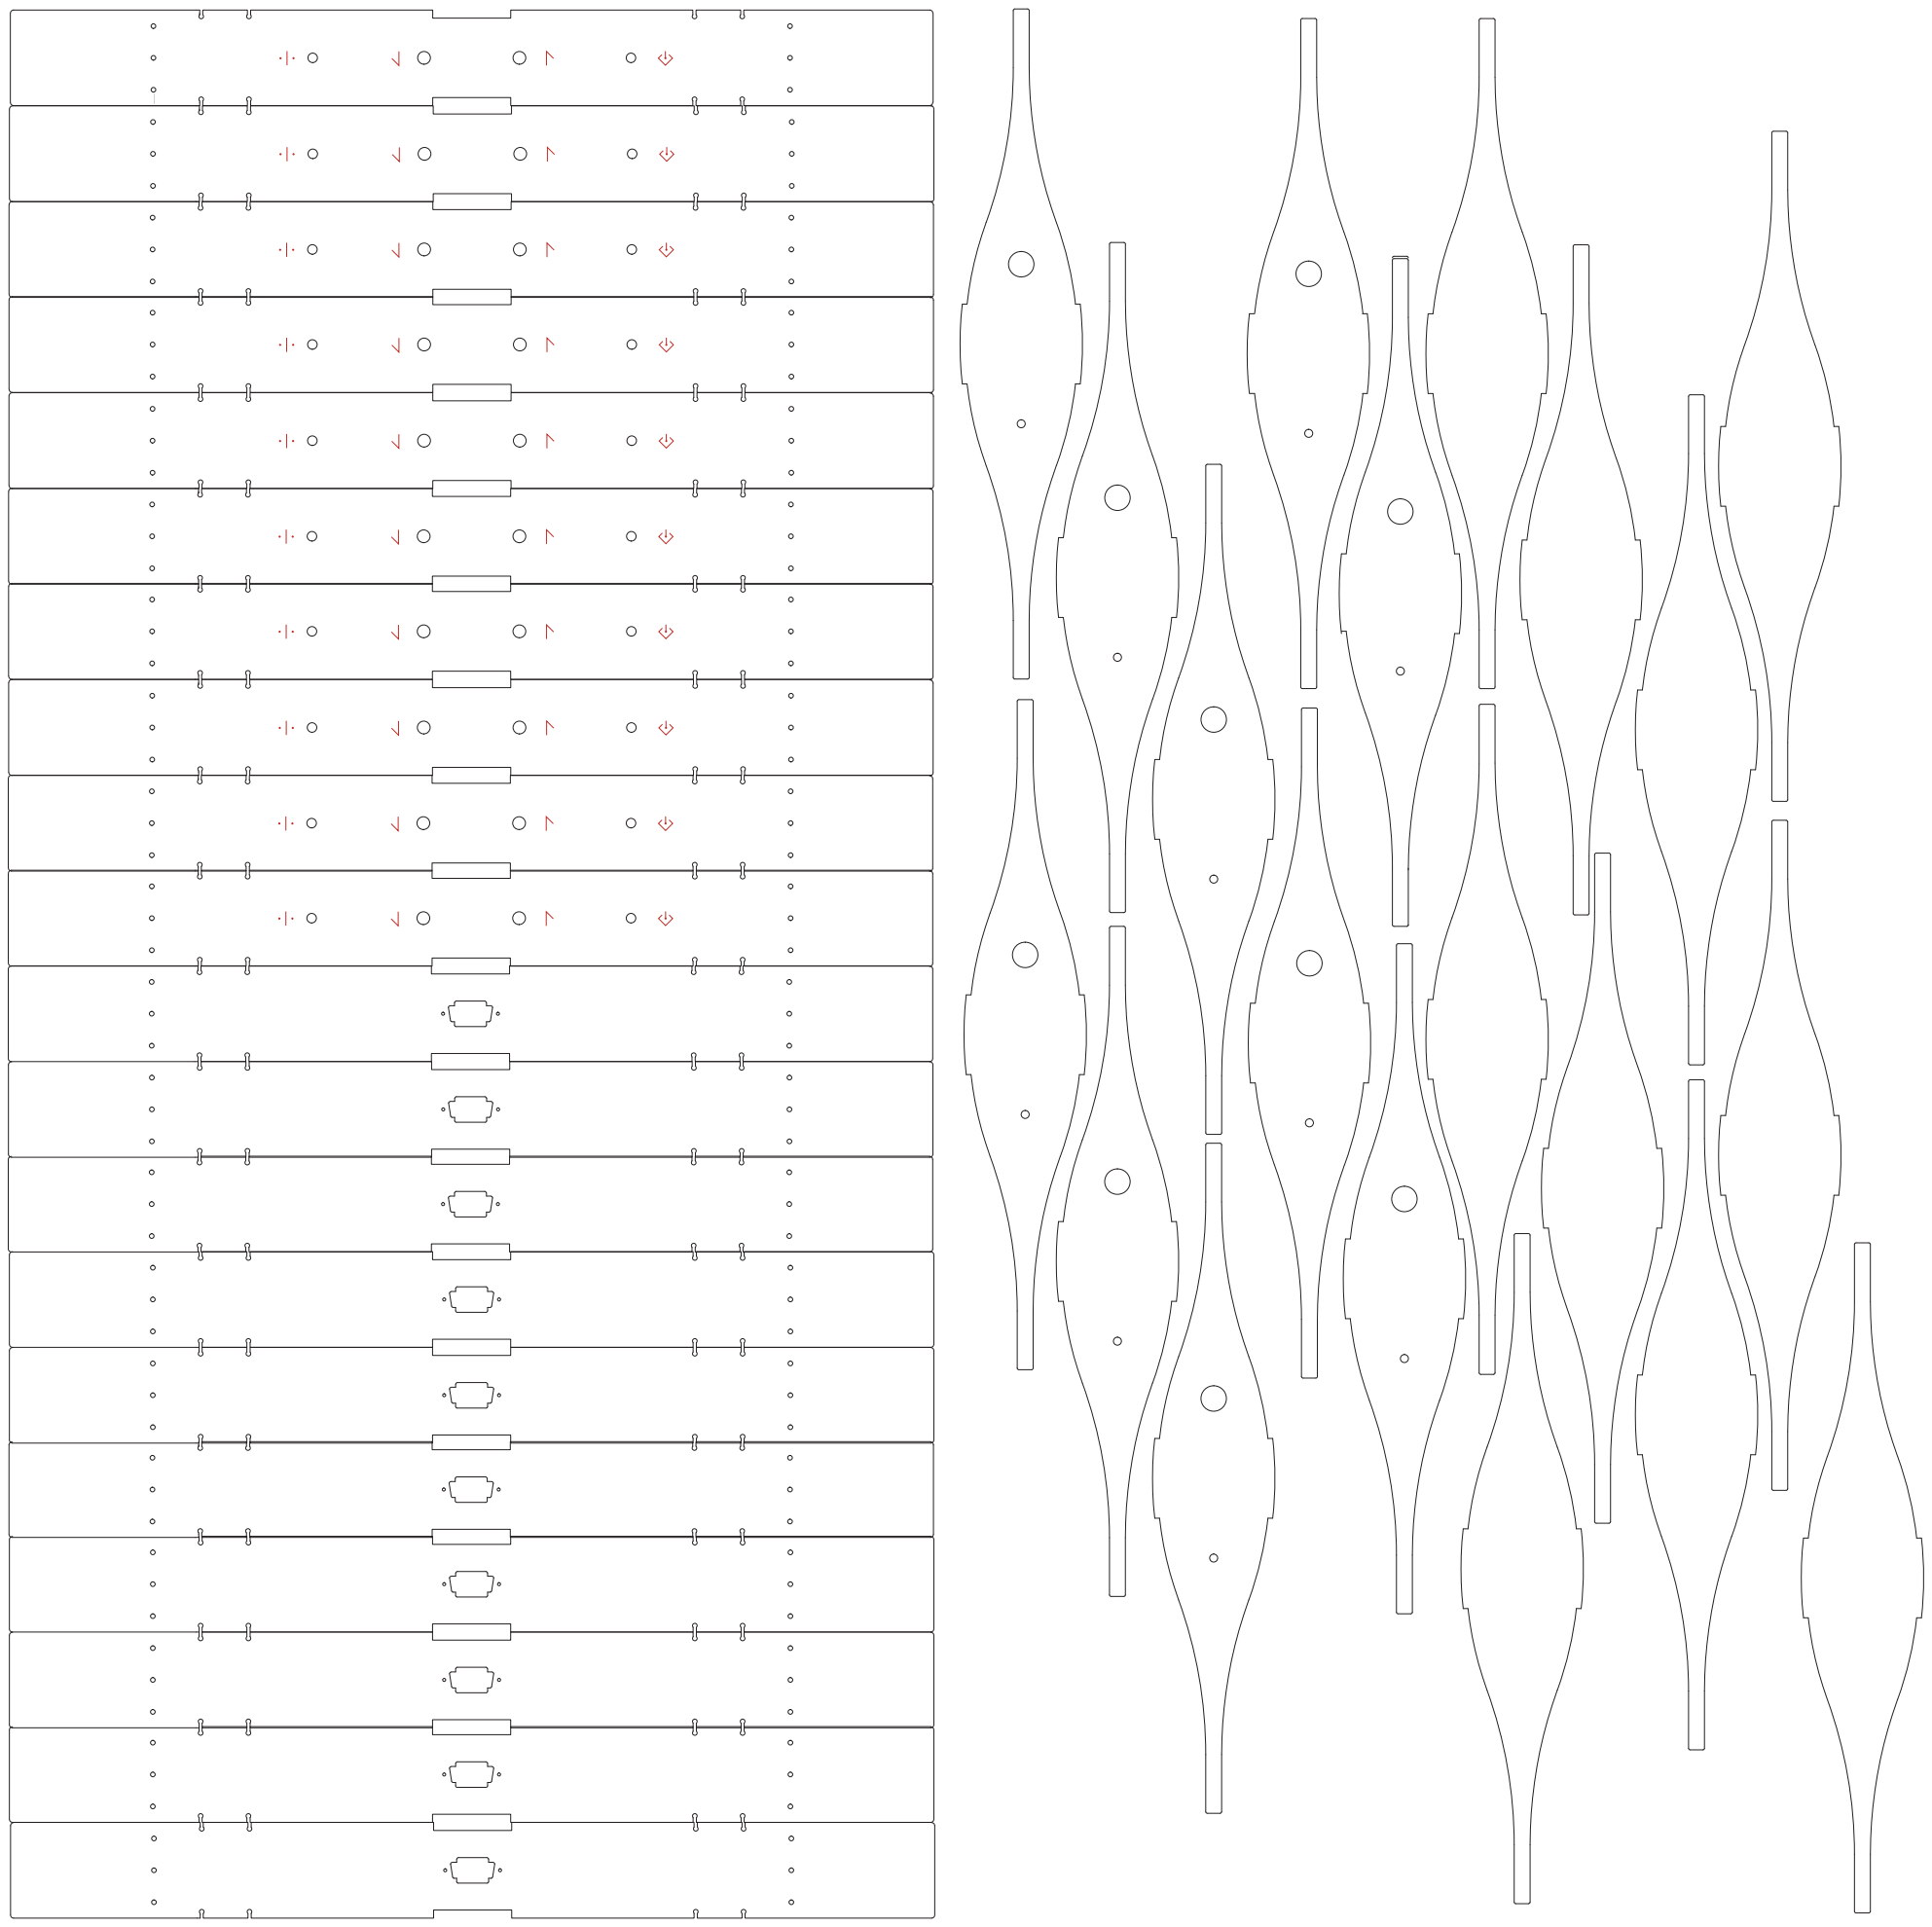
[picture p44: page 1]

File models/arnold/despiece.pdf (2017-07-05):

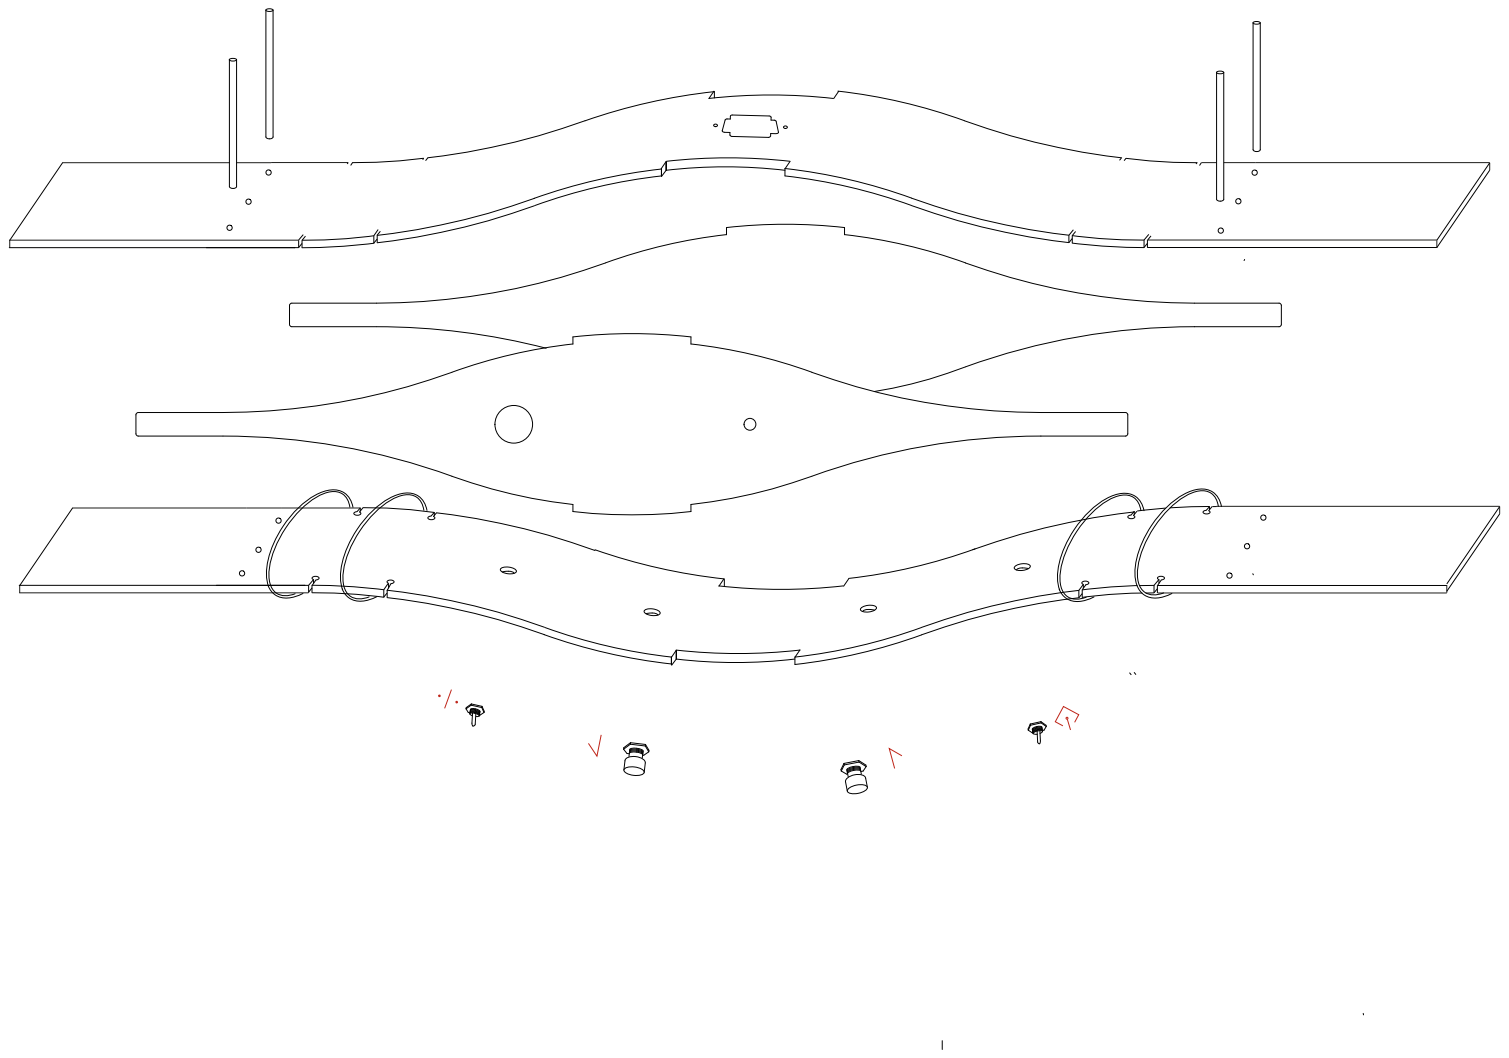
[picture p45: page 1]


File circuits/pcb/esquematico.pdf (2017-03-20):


CLK+/EN- BOTON RELOJ

19-03-2017 22:52 C:\Users\Cesar Cofre\Documents\eagle\MADLAB\MADLABar.sch (Sheet: 1/1)

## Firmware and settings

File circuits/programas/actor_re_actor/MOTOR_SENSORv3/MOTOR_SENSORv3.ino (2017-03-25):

#include <Stepper.h>
#include <AccelStepper.h>

/////////////////////// VARIBLES DE AJUSTE DE MEDIDAS (AJUSTAR) ////////////////////

int MINIMA_DISTANCIAcm=10;   //100minima distancia para medir
int MAXIMA_DISTANCIAcm=380;  //700maxima distancia para medir
int NUM_MAX_PASOS=2000;//23000 <-------------------DEFINIR AL COMIENZO DEL MONTAJE, es el número máximo de pasos entre una posicion inicial y una final
int x=0;
//////////////////////VARIABLES FIJAS DE CALCULO/////////////////////////////
int PPR=400;
int PASOS_DE_SEGURIDAD=50;  //50 holgura de pasos para la cantidad minima de pasos y la maxima
int MIN_PASOS_SEGUR= PASOS_DE_SEGURIDAD;
int MAX_PASOS_SEGUR= NUM_MAX_PASOS-PASOS_DE_SEGURIDAD;
int PASS=0;
int PASOS=0;  //variable calculada mapeando la distancia con el rango de pasos permitidos
int DIF_MIN_MEDIDAS=40;     //20variacion minima que debe existir entre dos medidas consecutivas para que actue el motor
////////////////////////// VARIABLES DEL MOTOR ////////////////////////////////

const int stepsPerRevolution = 800;  // pasos por rev
Stepper myStepper(stepsPerRevolution, 8, 9); // initialize the stepper library on pins 8 through 11:
AccelStepper stepper(2, 9, 8);   //LIB ACCEL

///////////////////VARIABLES SENSOR DE DISTANCIA////////////////////////////////////
float Inch=0.00;
int cm=0;
int cm_anterior=0;
int SonarPin=A0;
int sensorValue;
//////////////////BOTONES MANUALES////////////////////
int reloj=11;  //pin boton para accionar en sentido reloj
int antireloj=12;  //pin boton para accionar en sentido antireloj
int manual=3;  // pin boton manual
int led=13;    //led de modo manual o automatico
int R;    //variable de almacenamiento del boton RELOJ
int AR;   //variable de almacenamiento del boton ANTIRELOJ
boolean modo;
///////////////////VARIABLES DIMMER////////////////////
int AC_LOAD = 5;    // Output to Opto Triac pin
int full_dim=35;  // 5   maxima intensidad de luz
int empty_dim=95; //128  miniam intensidad de luz
int dimming = 128;  // Dimming level (0-128)  0 = ON, 128 = OFF
int A=full_dim;   //todo
int B=empty_dim;  //nada
int C=5;
int DIMMER=0;
int dimtime;
///////////////////////////////////////////////////////////
int VAR=0,DISTANCIA_CUERDA=0;
int RESULTADO=0;
///////////////////////////////////////////////////////////
void medicion()
{
   sensorValue=analogRead(SonarPin);
   Inch= (sensorValue*0.497);
   cm=Inch*2.54;
 
}
///////////////////////// DIMMER ////////////////////////////////////////
void zero_crosss_int()  //function to be fired at the zero crossing to dim the light
{
 // int dimtime = (75*dimming);    // For 60Hz =>65    
  delayMicroseconds(dimtime);    // Wait till firing the TRIAC    
  digitalWrite(AC_LOAD, HIGH);   // Fire the TRIAC
  delayMicroseconds(10);         // triac On propogation delay 
         // (for 60Hz use 8.33) Some Triacs need a longer period
  digitalWrite(AC_LOAD, LOW);    // No longer trigger the TRIAC (the next zero crossing will swith it off) TRIAC
}
/////////////////////////////////////////////////////////////////////////////////////////////////////////
void BOTON_MANUAL()  //interrupcion externa para el boton manual
{   
        
   detachInterrupt(0);  //desactiva la interrupcion attach
   digitalWrite(led,HIGH); //enciende el led para indicar modo manual
   delayMicroseconds(50);
   R=digitalRead(reloj); //lectura boton reloj
   AR=digitalRead(antireloj);  //lectura boton antireloj   
  /* if(!Serial.available())
   {
    if(VAR==0)
        {
         Serial.println("Ingrese distancia ha recoger de la cuerda en cm");
         VAR=1;
         }
     DISTANCIA_CUERDA=Serial.parseInt();
     RESULTADO=(DISTANCIA_CUERDA*800)/40;
     if(DISTANCIA_CUERDA!=0)
      {
        Serial.println();
        Serial.print("LOS PASOS QUE DEBE INGRESAR SON ");
        Serial.print(RESULTADO);
        Serial.println("  pasos");
        Serial.println();Serial.println("---------------------------");
        delay(1000);
      }
   }*/
   
 //  if(RESULTADO!=0 && modo==1){     
        if(AR==0 && R==0)
         {
          detachInterrupt(0);
          delay(100);
          medicion();
          Serial.print(cm);
          Serial.println(" cm ");
          }                       
       else if (AR==0 && R==1)
         {
          //detachInterrupt(0);
         // myStepper.step(100); //control por pasos
         // delayMicroseconds(700);
         
         stepper.setMaxSpeed(3000.0); //pasos por segundo
         stepper.setSpeed(3000.0); //pasos por segundo
         myStepper.step(100); //control por pasos
         delayMicroseconds(500);
         //stepper.runToNewPosition(x+200);//}
         //delay(1000);
        // x=0;
          
         }
       else if (AR==1 && R==0)
         {
          
         // detachInterrupt(0);
          //myStepper.step(-100);  //control por pasos
          //delayMicroseconds(1200);
          stepper.setMaxSpeed(3000.0); //pasos por segundo
          stepper.setSpeed(3000.0); //pasos por segundo
          myStepper.step(100); //control por pasos
          delayMicroseconds(500);
         // stepper.runToNewPosition(x+200);//}
         // delay(1000);
         // x=0;
          }
        
        R=digitalRead(reloj); //lectura boton reloj
        AR=digitalRead(antireloj);  //lectura boton antireloj
        modo=digitalRead(manual);                          
   //}
   R=digitalRead(reloj); //lectura boton reloj
   AR=digitalRead(antireloj);  //lectura boton antireloj
   modo=digitalRead(manual); 
}

///////////////////////////////////////////////////////////////////////////////////
void RANGO_DIM() //A=full_dim B=empty_dim C=5
{
  unsigned long CERO=0;
  if     (35<=DIMMER && DIMMER<45){unsigned long tiempo=millis();if((unsigned long)(tiempo-0)>=10){dimtime=2625;}} 
 // else if(40<=DIMMER && DIMMER<45){unsigned long tiempo=millis();if((unsigned long)(tiempo-CERO)>=10){dimtime=3000;}}
  else if(45<=DIMMER && DIMMER<55){unsigned long tiempo=millis();if((unsigned long)(tiempo-CERO)>=10){dimtime=3375;}}
 // else if(50<=DIMMER && DIMMER<55){unsigned long tiempo=millis();if((unsigned long)(tiempo-CERO)>=10){dimtime=3750;}}
  else if(55<=DIMMER && DIMMER<65){unsigned long tiempo=millis();if((unsigned long)(tiempo-CERO)>=10){dimtime=4150;}}
 // else if(60<=DIMMER && DIMMER<65){unsigned long tiempo=millis();if((unsigned long)(tiempo-CERO)>=10){dimtime=4500;}}
  else if(65<=DIMMER && DIMMER<75){unsigned long tiempo=millis();if((unsigned long)(tiempo-CERO)>=10){dimtime=4875;}}
 // else if(70<=DIMMER && DIMMER<75){unsigned long tiempo=millis();if((unsigned long)(tiempo-CERO)>=10){dimtime=5250;}}
  else if(75<=DIMMER && DIMMER<85){unsigned long tiempo=millis();if((unsigned long)(tiempo-CERO)>=10){dimtime=5625;}}
 // else if(80<=DIMMER && DIMMER<85){unsigned long tiempo=millis();if((unsigned long)(tiempo-CERO)>=10){dimtime=6000;}}
  else if(85<=DIMMER && DIMMER<95){unsigned long tiempo=millis();if((unsigned long)(tiempo-CERO)>=10){dimtime=6375;}}
 // else if(90<=DIMMER && DIMMER<95){unsigned long tiempo=millis();if((unsigned long)(tiempo-CERO)>=10){dimtime=6750;}}
  
}
///////////////////////////////////////////////////////////////////////////////////
void setup() 
{  
  pinMode(SonarPin,INPUT);
  Serial.begin(9600);
  stepper.setMaxSpeed(2000.0);  //LIB ACCEL
  myStepper.setSpeed(1000); // set the speed at 60 rpm:
  //stepper.setAcceleration(300.0);  //LIB ACCEL    
  pinMode(reloj,INPUT);
  pinMode(antireloj,INPUT);
  pinMode(manual,INPUT);
  pinMode(led,OUTPUT);

  pinMode(AC_LOAD, OUTPUT);// Set AC Load pin as output

 
}

////////////////////////////////////////////////////////////////////////////////////
////////////////////////////////////////////////////////////////////////////////////
////////////////////////////////////////////////////////////////////////////////////

void loop() 
{ 
                                     
  modo=digitalRead(manual);
  if(modo==0)  //MODO AUTOMATICO
  { 
   attachInterrupt(0, zero_crosss_int, RISING);                           
   digitalWrite(led,LOW);
   
   medicion();                  
   if(MINIMA_DISTANCIAcm<=cm && MAXIMA_DISTANCIAcm>=cm)  //mientras el sensor esté dentro de la distancia
    {     
     if(abs(cm_anterior-cm)>=DIF_MIN_MEDIDAS) //si la diferencia entre los ultimas 2 lecturas es mayor a DIF_MIN_MEDIDAS mostrarra cambio en motor y luz
        { 
          unsigned long CERO=0; 
          DIMMER=map(cm,MINIMA_DISTANCIAcm,MAXIMA_DISTANCIAcm,full_dim,empty_dim); 
          RANGO_DIM(); 
          PASOS=map(cm,MINIMA_DISTANCIAcm,MAXIMA_DISTANCIAcm,MAX_PASOS_SEGUR,MIN_PASOS_SEGUR);  //extrapola distancia con pasos
          unsigned long tiempo=millis();
          if((unsigned long)(tiempo-CERO)>=10)
           { 
           myStepper.setSpeed(5000);
           stepper.setAcceleration(5000.0);        
           stepper.runToNewPosition(PASOS);  //ejecuta la cantidad de pasos
           }   
                        
        }
    
     else if(MAXIMA_DISTANCIAcm+20 >= cm && cm >= MAXIMA_DISTANCIAcm-20 || MAXIMA_DISTANCIAcm+20 >= cm && cm >= MAXIMA_DISTANCIAcm-20)
            {
              unsigned long CERO=0; 
              dimtime=6750;
              unsigned long tiempo=millis();
              if((unsigned long)(tiempo-CERO)>=10)
                 {
                 attachInterrupt(0, zero_crosss_int, RISING); 
                 myStepper.setSpeed(5000);
                 stepper.setAcceleration(5000.0);        
                 stepper.runToNewPosition(0);  //ejecuta la cantidad de pasos
                 }                    
            }  
          
        }
       cm_anterior=cm;     
      // Serial.println(cm_anterior);
       
  }       
    
   else if(modo==1)
   {
     BOTON_MANUAL(); 
     modo=digitalRead(manual); 
    }                
  modo=digitalRead(manual);
}

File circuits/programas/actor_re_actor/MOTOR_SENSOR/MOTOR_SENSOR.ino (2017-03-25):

#include <Stepper.h>
#include <AccelStepper.h>
/////////////////////// VARIBLES DE AJUSTE DE MEDIDAS (AJUSTAR) ////////////////////

int MINIMA_DISTANCIAcm=20;   //sensor de distancia 
int MAXIMA_DISTANCIAcm=600;  //sensor de distancia
int DIF_MIN_MEDIDAS =15;     //variacion minima que debe haber entre dos medidas consecutivas para que actue el motor

int full_dim=30;  // 5   maxima intensidad de luz
int empty_dim=110; //128  miniam intensidad de luz

float CORDON_cm= 10; 

int NUM_MAX_PASOS=22000;// <-------------------DEFINIR AL COMIENZO DEL MONTAJE, desde una posicion inicial, es el numero máximo de pasos

//////////////////////VARIABLES FIJAS DE CALCULO/////////////////////////////
int PPR=400;    //PASOS POR REVOLUCION
float PERIMETROmm= 188.49;  //PERIMETRO RUEDA P=2*R*PI.....por vuelta avanza esto    

int cordon_pasos;
int PASOS_DE_SEGURIDAD=50;
int MIN_PASOS_SEGUR= PASOS_DE_SEGURIDAD;
int MAX_PASOS_SEGUR= NUM_MAX_PASOS-PASOS_DE_SEGURIDAD;

int exact_cm_value1=0;
int exact_cm_value2=0;
int condicion=0;
int PASOS=0;
int MEDIDAS[]={0,0};

////////////////////////// VARIABLES DEL MOTOR ////////////////////////////////

const int stepsPerRevolution = 800;  // pasos por rev
Stepper myStepper(stepsPerRevolution, 8, 9); // initialize the stepper library on pins 8 through 11:
AccelStepper stepper(2, 9, 8);   //LIB ACCEL

///////////////////VARIABLES SENSOR DE DISTANCIA////////////////////////////////////
int pw_pin=7;   //PIN UTILIZADO
int arraysize = 5;  //N° DE DATOS EN EL VECTOR (prog orig 9 datos)
int array[] = { 0, 0, 0, 0, 0};
long inch;   //variable de almacenamiento de pulgadas
int exact_cm_value;   //variable de almacenamiento de valores en cm

//////////////////BOTONES MANUALES////////////////////
int reloj=11;  //pin boton para accionar en sentido reloj
int antireloj=12;  //pin boton para accionar en sentido antireloj
int manual=3;  // pin boton manual
int led=13;    //led de modo manual o automatico
int R;    //variable de almacenamiento del boton RELOJ
int AR;   //variable de almacenamiento del boton ANTIRELOJ
int pot=A0;  //pin donde va conectado el pot para controlar el dimmer

///////////////////VARIABLES DIMMER////////////////////
int AC_LOAD = 5;    // Output to Opto Triac pin
int dimming = 128;  // Dimming level (0-128)  0 = ON, 128 = OFF

////////////////////////////////////////////////////////////
void sensorRead()   //se hace una lectura cada 10 miliseg de cuando pasa de high a low y lo divide por un factor
{
  for(int i = 0; i < arraysize; i++)
  {
  inch = pulseIn(pw_pin, HIGH);
  array[i] = inch/58;
  delay(1);
  }
  array_arrangment(array,arraysize);
  exact_cm_value= filter(array,arraysize);  //VARIABLE EN CENTIMETROS DE LA DISTANCIA
}
//////////////////////////////////////////////////////////////
void array_arrangment(int *a,int n)
{
  for (int i = 1; i < n; ++i)
    {
      int j = a[i];
      int k;
      for (k = i - 1; (k >= 0) && (j < a[k]); k--)
        {
        a[k + 1] = a[k];
        }
      a[k + 1] = j;
    }
}
//////////////////////////////////////////////////////////////
int filter(int *a,int n)
{
    int i = 0;
    int count = 0;
    int maxCount = 0;
    int filter = 0;
    int median;
    int prevCount = 0;
    while(i<(n-1))
    {
        prevCount=count;
        count=0;
        while(a[i]==a[i+1])
          {
          count++;
          i++;
          }
        if(count>prevCount && count>maxCount)
          {
          filter=a[i];
          maxCount=count;
          median=0;
          }
        if(count==0)
          {
          i++;
          }
        if(count==maxCount)
          {//If the dataset has 2 or more modes.
          median=1;
          }
        if(filter==0||median==1)
          {//Return the median if there is no mode.
          filter=a[(n/2)];
          }        
        return filter;    
    }
}
///////////////////////// DIMMER ////////////////////////////////////////

//the interrupt function must take no parameters and return nothing
  // Firing angle calculation : 1 full 50Hz wave =1/50=20ms 
  // Every zerocrossing thus: (50Hz)-> 10ms (1/2 Cycle) 
  // For 60Hz => 8.33ms (10.000/120)
  // 10ms=10000us
  // (10000us - 10us) / 128 = 75 (Approx) For 60Hz =>65
  
void zero_crosss_int()  //function to be fired at the zero crossing to dim the light
{
  int dimtime = (75*dimming);    // For 60Hz =>65    
  delayMicroseconds(dimtime);    // Wait till firing the TRIAC    
  digitalWrite(AC_LOAD, HIGH);   // Fire the TRIAC
  delayMicroseconds(10);         // triac On propogation delay 
         // (for 60Hz use 8.33) Some Triacs need a longer period
  digitalWrite(AC_LOAD, LOW);    // No longer trigger the TRIAC (the next zero crossing will swith it off) TRIAC
}

////////////////////////////////////////////////////////////////////////////////////
///////////////////////////////////////////////////////////////////////////////////
///////////////////////////////////////////////////////////////////////////////////
void setup() 
{  
  myStepper.setSpeed(200); // set the speed at 60 rpm:
  pinMode(pw_pin, INPUT);  //definición del pin sensor
  Serial.begin(9600);
  stepper.setMaxSpeed(6000.0);  //LIB ACCEL
  stepper.setAcceleration(6000.0);  //LIB ACCEL
  
  pinMode(reloj,INPUT);
  pinMode(antireloj,INPUT);
  pinMode(manual,INPUT);
  pinMode(led,OUTPUT);

  pinMode(AC_LOAD, OUTPUT);// Set AC Load pin as output
  attachInterrupt(0, zero_crosss_int, RISING);  // Choose the zero cross interrupt # from the table above
  cordon_pasos= (CORDON_cm*PPR)/(PERIMETROmm*10) ; // CALCULO dependiendo de los centrimetros ingresados en CORDON_cm calcula la cantidad de pasos
}

////////////////////////////////////////////////////////////////////////////////////
////////////////////////////////////////////////////////////////////////////////////
////////////////////////////////////////////////////////////////////////////////////
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

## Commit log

2017-03-14 modelo iam
    [case-motor.iam]
2017-03-19 avance domingo 19
    [Carrete Impreso.0004.ipt, Carrete Impreso.0005.ipt, Carrete Impreso.ipt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]
2017-03-20 avance dibujos lunes 20
    archivos de corte
    [Caja actor-re-actor engranes acrílicos.iam, Caja actor-re-actor.iam, Carcasa.ipt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]
2017-03-20 electronics files
    esquemas, programas y pcb
2017-03-21 avances dibujos lunes 20
    modelo final de carcasa
    [Carcasa.0013.ipt, Carcasa.ipt, Desarrollo carcasa.dxf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]
2017-03-22 avance dibujos martes 21
    [Carcasa.ipt, Case-D.iam, Desarrollo carcasa.dxf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]
2017-03-23 avances dibujos miercoles 23
    [Desarrollo carcasa.dxf, carca.dxf, carrete_base8mm.stl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]
2017-03-25 de engranes a correas
    [CCB Bandeja.dxf, CCB RefuerzoU.dxf, CCB T1.dxf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]
2017-03-25 vjhlk
    khñioj
    [project.cfg]
2017-03-27 avances dibujo domingo 26
    [Caja motriz 1_engranajes rectos.0026.iam, Caja motriz 1_engranajes rectos.iam, Caja motriz 2.0003.iam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]
2017-03-28 Stepper driver
    mapping sensor to motor with simple library
2017-03-29 programas de prueba
    en carpeta programas de base
2017-03-29 v3-hspencer con más torque
    logré tener mayor torque pero gira sólo hacia un solo lado y la
    reacción no es muy buena….
2017-03-31 versión 3 con torque
2017-04-03 avances dibujos
    variaciones para la caja que se instaló en casa central, falta acualizar
    algunas bibliotecas que quedaron en otro computador
    [Caja motriz 2.iam, Caja motriz 2_correa dentada.iam, Potencia2.iam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]
2017-04-03 Revert "avances dibujos"
    This reverts commit 0eb5dd6d8c662058200520306803f999c25904a2.
    [Caja motriz 2.iam, Caja motriz 2_correa dentada.iam, Potencia2.iam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]
2017-04-03 Revert "Revert "avances dibujos""
    This reverts commit b2d5ba400d0f0a51e7c0014bf34766f8875e8eed.
    [Caja motriz 2.iam, Caja motriz 2_correa dentada.iam, Potencia2.iam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]
2017-04-03 ajustes para mayor torque
2017-04-04 versión estable optimizada
    se modifica la lógica del programa para que complete los trabajos de ir
    a un objetivo de forma consecutiva
2017-07-05 archivos arnold
    [pieza baja - documenta.ipt, pieza frontal - documenta.ipt, pieza superior - documenta.ipt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]
